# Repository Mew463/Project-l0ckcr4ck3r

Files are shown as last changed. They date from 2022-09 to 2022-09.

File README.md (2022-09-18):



# Project-l0ckcr4ck3r
This robot is a true creation of the idea many years ago brought on by [Samy Kamkar's robot](https://samy.pl/combobreaker/) that "utilized" his algorithm for cracking combination locks. Samy Kamkar never demonstrated his robot actually performing the algorithm, though he implied multiple times that it does do it.

I've always wanted to build a robot that actually decodes locks while maintaining a cool desk toy vibe! I am quite happy with the user-oriented design and doubles as a nice fidgety-toy-thing to play with.  

This robot is able to decode the majority of locks that don't have much wear and tear on it and usually takes ~40 seconds.

<br/><br/>

## Photo
MVIMG_20220913_114445

## Video
3 Locks in a Row (https://www.youtube.com/watch?v=nw5f3ZPQd-o)

# How it works. 
## Cracking lock Algorithm 
First number: Turn dial Counter Clockwise while incrementally adding more and more force to the shackle until it suddenly stops. Round down to the nearest whole number and add 14. That is the first number in the combo. 

Third number: 
1) Find the gates between digits 0 - 10 . 
2) Take the two gates that correspond to a whole number and see whether each of those numbers %(modulo) 4 = firstNum % 4. 
3) If the equation is satisfied, store that number somewhere. Now add 10 to each number and perform the same operation as the previous step until you have **two** numbers that satisfy the equation
4) Now check the gate size of the two numbers which satisfy the equation. The number with the biggest gate is the third number. 

Second number: Guess and check until the lock opens, though it follows a pattern of being (FirstNum % 4) + a multiple of 4.

I found that this [video](https://www.youtube.com/watch?v=27rE5ZvWLU0&ab_channel=HelpfulLockPicker) really helped me when trying to program the algorithm.

## This robot 
A TMC2208 Trinamic driver drives a stepper motor & magnetic encoder. These components turn the dial and can detect when the stepper motor stalls. 
L0ckcr4ck3r (6)

With this method, any desired number can easily be input into the lock and the lock can be "felt" for it's geometries.
ezgif com-gif-maker (4)

Meanwhile a servo powers a rack and pinion gear which allows precise control of the shackle.
ezgif com-gif-maker

Since I modified the servo with an [analog Feedback wire](https://www.youtube.com/watch?v=XfZLtkr6dgU&ab_channel=CuriousMotor), we can pull up on the shackle and use this to check whether the lock has been opened or not. 

ezgif com-gif-maker (6)

# 3D Model
L0ckcr4ck3r
[CAD Files](https://cad.onshape.com/documents/2b977856993104d0f24f1470/w/e2828f2601c6a316a05788e0/e/a76e54aa91df89bb32ae0012)

# Electronics 
Custom PCB powered by a 12V USB C input. An Arduino Nano is the brain and a 5V regulator gives the neccessary voltage for the servo. 
MVIMG_20220823_125722
l0ckcr4ck3r
Electronics

KiCAD files are included in the github. 

# Materials

## Mechanical
* [TMC2208 Stepper Driver](https://www.amazon.com/Printer-TMC2208-Screwdriver-Controller-Ramps1-4/dp/B082LSQWZF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)
* [High torque servos](https://www.amazon.com/Youleke-Torque-Digital-Servo%EF%BC%8CWaterproof-Horn%EF%BC%88270%C2%B0%EF%BC%89/dp/B08739MGPL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)
* [Stepper motor](https://www.amazon.com/STEPPERONLINE-Bipolar-Stepper-22-6oz-Extruder/dp/B00PNEQ79Q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)
* [AS5600 Magnetic Encoder](https://www.amazon.com/Magnetic-Encoder-Induction-Measurement-Precision/dp/B094F8H591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)
* Assorted M3 Bolts

## Electrical
* Arduino Nano
* 10uF Capacitor x2
* Diode 
* [5V Regulator](https://www.digikey.com/en/products/detail/stmicroelectronics/LD1085V50/669220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)
* [OLED Display](https://www.amazon.com/Self-Luminous-Display-Compatible-Arduino-Raspberry/dp/B09JWN8K99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)
* [Rotary Encoder](https://www.amazon.com/Taiss-KY-040-Encoder-15%C3%9716-5-Arduino/dp/B07F26CT6B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)
* [Blower Fan](https://www.amazon.com/WINSINN-Bearings-Brushless-Cooling-40mm20mm/dp/B08R9JJZ5Z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)
* [USB C 12V ](https://www.amazon.com/MELIFE-Type-C-Voltage-Trigger-Module/dp/B0953G14Q2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)
* [Power Supply](https://www.amazon.com/ZMI-zPower-Turbo-Power-Adapter/dp/B07D64QLQ1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)

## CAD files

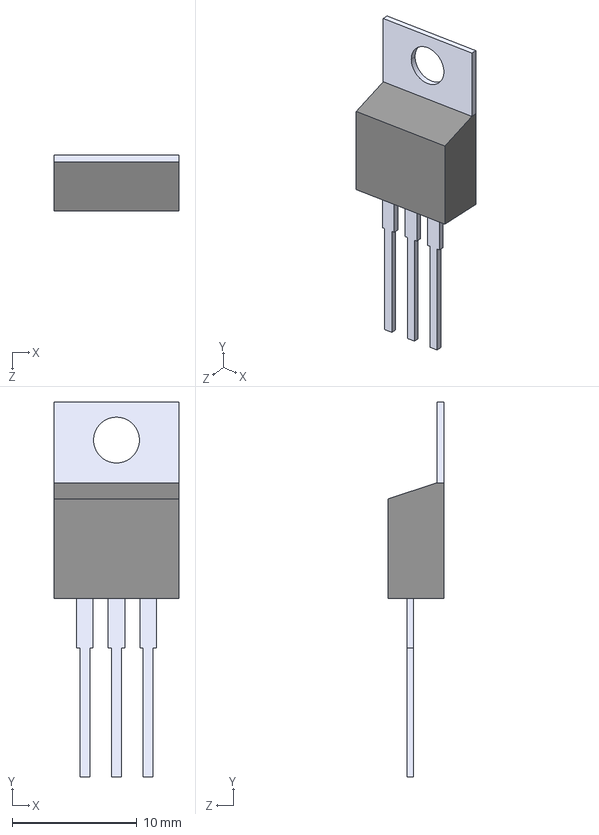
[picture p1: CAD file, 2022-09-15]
l0ckcr4ck3r pcb/LD1085V50/LD1085V50.step
9.97 x 30.0 x 4.44 mm

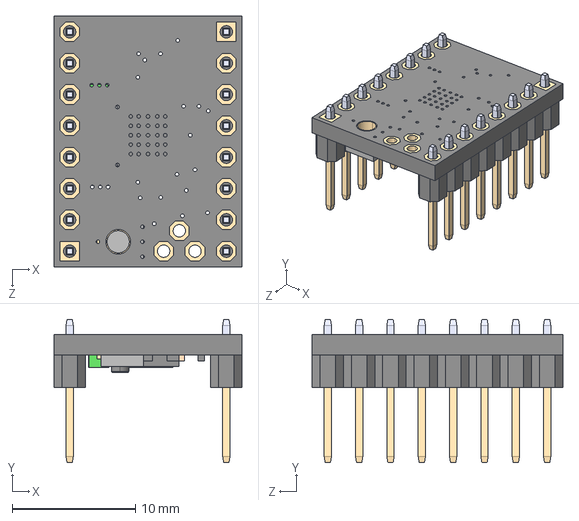
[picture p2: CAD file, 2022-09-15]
l0ckcr4ck3r pcb/TMC2208_SILENTSTEPSTICK/TMC2208_SILENTSTEPSTICK.step
15.2 x 11.6 x 20.3 mm

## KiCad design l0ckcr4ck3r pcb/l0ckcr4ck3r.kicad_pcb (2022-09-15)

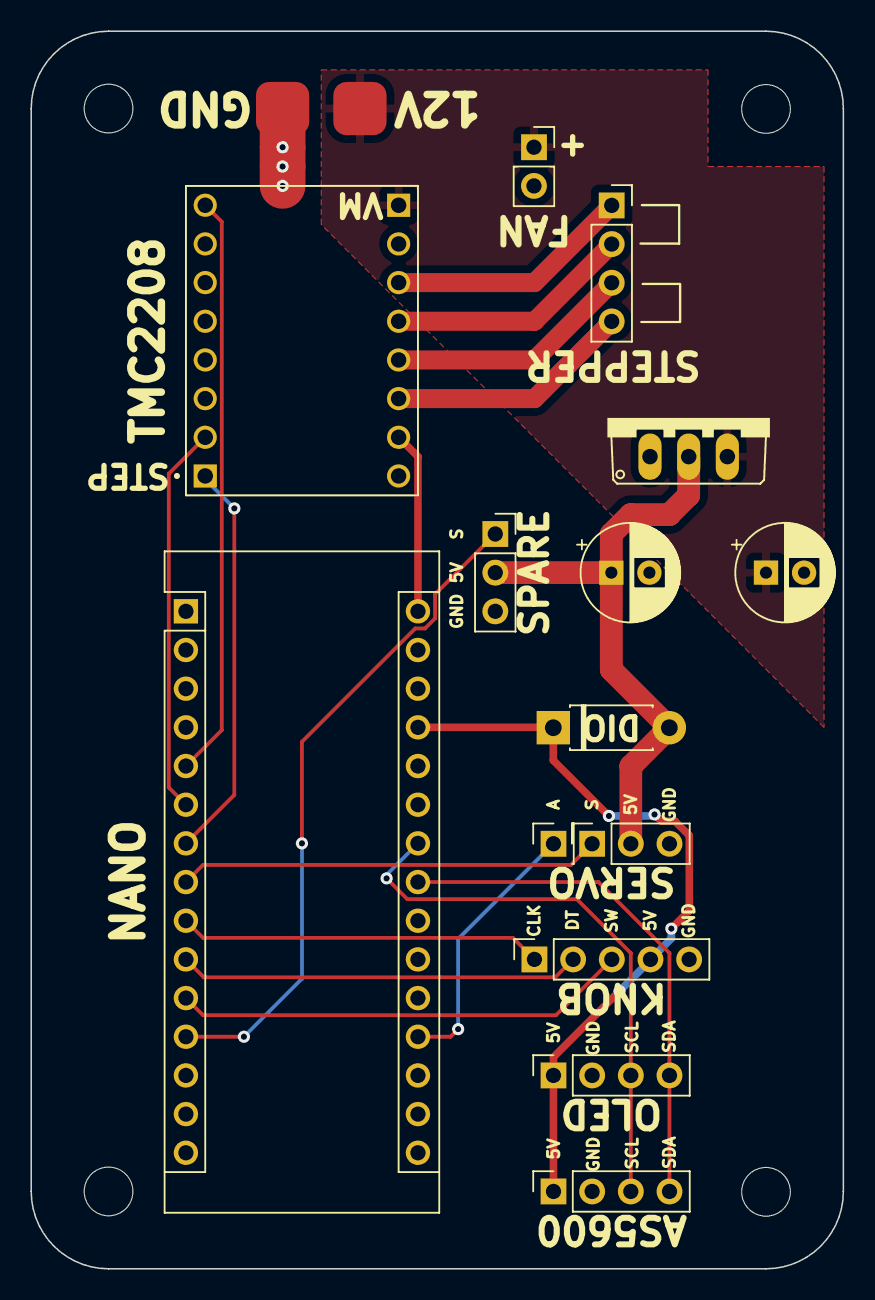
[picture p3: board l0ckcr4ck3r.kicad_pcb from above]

Board: 2 copper layers, 53.3 x 81.3 mm, 15 parts (0 on the bottom side), 20 nets.

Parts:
A1: Arduino_Nano_v3.x; Arduino_Nano
C1, C2: 10uF; CP_Radial_D6.3mm_P2.50mm
D1: 1N4002; D_DO-41_SOD81_P7.62mm_Horizontal
J1: Servo Feedback; PinSocket_1x01_P2.54mm_Vertical
M1: Stepper_Motor_bipolar; PinSocket_1x04_P2.54mm_Vertical
M2: Fan; PinSocket_1x02_P2.54mm_Vertical
M3: Motor_Servo; PinSocket_1x03_P2.54mm_Vertical
M4: Spare; PinSocket_1x03_P2.54mm_Vertical
U1: PowerIn; PowerPads
U2: TMC2208_SILENTSTEPSTICK; MODULE_TMC2208_SILENTSTEPSTICK
U3: Encoder; PinSocket_1x05_P2.54mm_Vertical
U4: LD1085V50; TO220V
U5: AS5600; PinSocket_1x04_P2.54mm_Vertical
U6: OLED Display; PinSocket_1x04_P2.54mm_Vertical

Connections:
+5V: A1.27 (+5V), D1.1 (K), U3.4 (+), U5.1 (VCC), U6.1 (VCC)
+12V: C2.1, M2.1 (+), U1.1 (12V), U2.JP2_1 (VM), U4.3 (Input)
CLK: A1.9 (D6), U3.1 (CLK)
D5: A1.8 (D5), M3.1 (PWM)
D9: A1.12 (D9), M4.1 (PWM)
DT: A1.10 (D7), U3.2 (DT)
GND: A1.4 (GND), A1.29 (GND), C1.2, C2.2, M2.2 (-), M3.3 (-), M4.3 (-), U1.2 (GND), U2.JP2_2 (GND), U2.JP2_8 (GND), U3.5 (GND), U4.1, U5.2 (GND), U6.2 (GND)
unnamed: A1.5 (D2), U2.JP1_8 (EN)
unnamed: A1.6 (D3), U2.JP1_2 (STEP)
unnamed: A1.7 (D4), U2.JP1_1 (DIR)
unnamed: A1.19 (A0), J1.1
unnamed: A1.30 (VIN), U2.JP2_7 (VIO)
unnamed: C1.1, D1.2 (A), M3.2 (+), M4.2 (+), U4.2
unnamed: M1.1, U2.JP2_3 (OA2)
unnamed: M1.2 (-), U2.JP2_4 (OA1)
unnamed: M1.3, U2.JP2_5 (OB1)
unnamed: M1.4, U2.JP2_6 (OB2)
SCL: A1.24 (A5), U5.3 (SCL), U6.3 (SCL)
SDA: A1.23 (A4), U5.4 (SDA), U6.4 (SDA)
SW: A1.11 (D8), U3.3 (SW)

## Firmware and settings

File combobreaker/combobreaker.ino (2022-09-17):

#include <AccelStepper.h>
#include "AS5600.h"
#include "Wire.h"
#include "Servo.h"
#include "FastLED.h"
#include <U8x8lib.h>
#include "Button2.h"; //  https://github.com/LennartHennigs/Button2
#include "ESPRotary.h";

#define ROTARY_PIN1  6
#define ROTARY_PIN2 7
#define BUTTON_PIN  8

#define CLICKS_PER_STEP   4  

String mainMenu[] = {"Cracklock", "Auto Dialer", "Reset Motors", "Disable Step", "end", "Main Menu"};
String AutoDial[] = {"Back", "end", "Auto Dialer"};
int page = 0;
int selection = -1;
int curLockSett = 1;
int positionencoder;
int lastenc;

ESPRotary r = ESPRotary(ROTARY_PIN1, ROTARY_PIN2, CLICKS_PER_STEP);

U8X8_SH1106_128X64_NONAME_HW_I2C u8x8(U8X8_PIN_NONE);

#define offset 788 // Offset value gotten from readAngle()
#define stepsperRev 1600

#define servoNeutral 1900 // Point when shackle is fully pushed INTO THE LOCK
#define servoOpen 1500
#define servoFeedbackOpen 346

bool checkTwice = false;
bool cracked = false;
bool estop = false;
bool firstCheckStall = false;
bool firstComboCheck = true;
bool mtrsReset = true;
enum DIR{CC, CW, CLOSE};

AccelStepper stepper(1,3,4); // STEP, DIR 
int enablePin = 2;
AS5600 as5600;  //  use default Wire

double gateBounds[2];

Servo servo;
const int servofeedback = A0;

unsigned long lockTime;

// Related to each lock!! for testing!!
int gateHeight = 1798;
int firstNum = 0;
int firstNumRem;
int thirdNum[] = {-1, -1, -1, -1}; 
int secondNums[4][8];
//

void dial(float num, DIR _dir = CLOSE, int extraRot = 0);
float readLockNum(int num = -1);
void crackLock();

int showmenuItems(String items[], bool forcereset = false);
bool findBounds(bool checkSkip = 0);
bool testAllCombos(int ind = 0);


void setup()
{  
  Serial.begin(9600);

  u8x8.begin();
  r.setChangedHandler(rotate);
  r.setLeftRotationHandler(showDirection);
  r.setRightRotationHandler(showDirection);

  stepper.setMaxSpeed(10000);
  stepper.setAcceleration(100000);

  pinMode(enablePin, OUTPUT);
  digitalWrite(enablePin, LOW); //Enable motor driver

  servo.attach(5);
  servo.writeMicroseconds(servoNeutral);
  dial(0);
  pinMode(servofeedback, INPUT);

  Wire.begin();
  as5600.begin(4);  //  set direction pin.
  as5600.setDirection(AS5600_COUNTERCLOCK_WISE);  // default, just be explicit.

  u8x8.setFont(u8x8_font_chroma48medium8_r);
  u8x8.drawString(0,0,"Project");
  u8x8.drawString(0,1,"l0ckcr4ck3r");
  u8x8.drawString(0,4,"By Mu");
  delay(1000);
  u8x8.clearDisplay();

}

void loop()
{  
  
  
  switch (page) {
    case 0:
      
      selection = showmenuItems(mainMenu);

      switch (selection) {
      case 0:
        u8x8.clear();
        u8x8.drawString(0,0, "Lock Cracker");
        crackLock();
        while (!digitalRead(BUTTON_PIN));
        showmenuItems(mainMenu, true);
        break;
      case 1:
        u8x8.clear();
        u8x8.drawString(0,0, "Auto Dialer");
        u8x8.drawString(3,4, "Current");
        u8x8.drawString(0,2, "<");
        u8x8.drawString(2,2, "Back");
        page = 1;
        break;
      case 2:
        dial(0);
        servo.writeMicroseconds(servoNeutral);
        mtrsReset = true;
        break;
      case 3:
        digitalWrite(enablePin, HIGH);
        break;
      }
      break;

    case 1:
      r.loop();
      u8x8.setCursor(3, 6);
      u8x8.print(readLockNum());
      if (lastenc != positionencoder)
        dial(positionencoder%40);
      lastenc = positionencoder;
      if (detectPress()) {
        showmenuItems(mainMenu, true);
        page = 0;
      }
      break;

  }
  
  
}

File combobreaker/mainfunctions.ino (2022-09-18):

void findFirstNum() { // Spins the dial while slowly pulling up on the shackle, when the motor stalls add ~14 to the current number
  printLine("Finding", 2);
  printLine("First Num", 3);
  int curServoCom = servoNeutral - 60; // Start probing a little higher than Neutral to save time
  dial(0, CC, 2); // Clear lock and ensure all the dials are being spun

  servo.writeMicroseconds(curServoCom);

  while (true) {
    EVERY_N_SECONDS(1) 
      servo.writeMicroseconds(curServoCom-=2); // Slowly increase tension on the shackle

    double stallnum = returnStallNum(1500, 20);
    if (stallnum != -1) { // if stall detected
      stallnum -= .2;
      servo.writeMicroseconds(servoNeutral); 
      delay(100);
      gateHeight = curServoCom;
      Serial.println("Stalled at: " + String(stallnum));
      stallnum = (int)stallnum + 14; // Round down the number of interest and add 14
      if (stallnum > 40) // Wrap around case
        stallnum-=40;
      firstNum = stallnum;
      break;
    }
  }
  Serial.println("First number: " + String(firstNum) + " GateHeight : " + String(gateHeight));
}

void findThirdNum() {
  int lockedPos[3] = {-1, -1, -1};
  int posThirdNums[2];
  double gateSize[2];

  double gateDifferences[3];
  double NOI[3];


  int lcrossover;
  int rcrossover;
  int x = 0;

  printLine("Third Num", 3);

  dial(39.5); // Setup lock dial to intiate probing 
  firstNumRem = firstNum % 4;

  for (int i = 0; i < 3; i++) { // Never need to check more than the first 3 gates of the lock
      if (!digitalRead(BUTTON_PIN) || estop) {
        estop = 1;
        return;
      }
      if (i == 0) {
        if (findBounds(1) == 0) {
          Serial.println("Skip detected!");
          firstCheckStall = false;
          dial(1.5);
          findBounds();
        }
      } 
      else
        findBounds();

      if (gateBounds[0] > 20 && gateBounds[1] > 20) { // Did not cross over past 0 which can't be a number of interest
        dial(gateBounds[1] + 2, CLOSE); // Move onto the next gate, which is two numbers from the right edge of the previous gate 
        i = -1;
        Serial.println("Skipping as the number did not cross 0");
        continue;
      }
      
      lcrossover = int(gateBounds[0]) + 1; // lcrossover and rcross over should be the same 
      rcrossover = int(gateBounds[1]); 

      if (gateBounds[0] > 20) {
        lcrossover = 0;
        gateBounds[0] -= 40;
      }

      double diffl = abs(lcrossover - gateBounds[0]);
      double diffr = abs(rcrossover - gateBounds[1]); 

      if (lcrossover != rcrossover) {
        if (diffl > diffr)
          NOI[i] = lcrossover;
        else
          NOI[i] = rcrossover;
      }
      else
        NOI[i] = lcrossover;

      Serial.println("DiffL: " + String(diffl) + "\t DiffR: " + String(diffr) + " NOI : " + String(NOI[i]));

      if (diffl < diffr)
        gateDifferences[i] = diffl;
      else
        gateDifferences[i] = diffr;
      
      if (i != 2)
        dial(gateBounds[1] + 2.5, CLOSE); // Move onto the next gate, which is two numbers from the right edge of the previous gate 
    }

    double greatest = 0;
    int ind;
    double tolCheck[2];
    bool stop = false;
    checkTwice = false;
    for (int z = 0; z < 3; z++) {

      if (z == 1) { // Tolerance check. If the second greatest gateDifferences are within a certain tolerance, calculate all possibilties
        int p = 0;
        for (int i = 0; i < 3; i++)
          if (gateDifferences[i] != -1)
            tolCheck[p++] = gateDifferences[i];
        if (abs(tolCheck[1] - tolCheck[0]) < 0.1) {
          Serial.println("Using 3 lockedPositions since Tolerance check actviated");
          checkTwice = true;
        }
      }

      for (int i = 0; i < 3; i++) {
        if (gateDifferences[i] > greatest) {
          greatest = gateDifferences[i];
          ind = i;
        }
      }
      lockedPos[z] = NOI[ind];
      gateDifferences[ind] = -1; // Reset it to make sure to not choose it again
      greatest = 0;
    }

    Serial.println("Locked Positions : " + String(lockedPos[0]) + " " + String(lockedPos[1]));
    if (checkTwice)
      Serial.println("Locked Positions : " + String(lockedPos[0]) + " " + String(lockedPos[2]));

  printLine("Testing", 2);
  printLine("Gate Size : ", 3);

  if (!digitalRead(BUTTON_PIN) || estop) {
    estop = 1;
    return;
  }


  x = 0;
  int a = 0;

  for (int i = 0; i < 4; i++) {  // Check all combinations to see if the modulus matures with the modules of the first Num 
    if (lockedPos[0] % 4 == firstNumRem)
      posThirdNums[x++] = lockedPos[0];
    if (lockedPos[a+1] % 4 == firstNumRem)
      posThirdNums[x++] = lockedPos[a+1];
    if (x > 1)
      break;

    lockedPos[0] += 10; lockedPos[a+1] += 10; //increment both numbers by 10 to check all combinations

  }

  for (int i = 0; i < 2; i++) { // Narrow it down from two numbers to one number by choosing the largest gate size
    u8x8.drawString(12, 3,"  ");
    u8x8.setCursor(12, 3);
    u8x8.print(posThirdNums[i]);
    if (posThirdNums[i] > 40) {
      estop = 1;
      return;
    }
    dial(posThirdNums[i], CC); 
    findBounds();

    double diff = gateBounds[1] - gateBounds[0];
    if (diff < 0) // Handle wrap around
      diff += 40;
    gateSize[i] = diff;
  }

  if (gateSize[0] > gateSize[1]) {
    thirdNum[a] = posThirdNums[0];
    thirdNum[a+2] = posThirdNums[1]; // Keep track of the other one as well
  }
  else {
    thirdNum[a] = posThirdNums[1];
    thirdNum[a+2] = posThirdNums[0]; // Keep track of the other one as well
  }

  Serial.println("Third number: " + String(thirdNum[a]));  

}

void calcSecondNums() { // Calculates the possible second numbers and places them in the array
  firstNumRem = firstNum % 4;
  
  for (int d = 0; d < 4; d++) {
    int z = 0;
    int curCheck = firstNumRem + 2;
    // Serial.println(thirdNum[0]);
    for (int i = 0; i < 10; i++) { // If the number is 2 or less away from the first number, we can disregard it
      if (abs(curCheck - thirdNum[d]) > 3 && abs(curCheck - thirdNum[d]) < 38 && thirdNum[d] != -1) {
        secondNums[d][z++] = curCheck;
      }
      curCheck += 4;
      if (curCheck > 40) // Handles wrap around 
        curCheck -= 40;
    }
  }

  // Serial.println("secondNums array: ");
  // for (int i = 0; i < 8; i++) 
  //   Serial.print(String(secondNums[0][i]) + "\t");
  // Serial.println();

  
  
}
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

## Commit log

2022-09-01 added feedback during lock cracking
    [GUI.ino, combobreaker.ino, helperfunctions.ino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]
2022-09-02 started on the error case where the start lifting up on a gate for finding third number
    [combobreaker.ino, mainfunctions.ino]
2022-09-15 added kicad and gif
    [LD1085V50.step, TMC2208_SILENTSTEPSTICK.step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]
2022-09-17 updated some servo values
2022-09-18 fixed bug with 11-13-39 lock
    [cracklock.ino, mainfunctions.ino]
